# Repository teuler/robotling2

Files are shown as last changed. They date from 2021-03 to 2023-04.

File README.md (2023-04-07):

# Robotling 2

Robotling-2 is a small, simple 6-legged robot using the new Raspberry Pi micro controller [RP2040](https://www.raspberrypi.org/documentation/rp2040/getting-started/) as brain. To move around, it uses a simplified tripod walk that requires only three servo motors - inspired by a 20 year old book called ["Insectronics"](https://books.google.de/books/about/Insectronics.html?id=dYZ-67WxUWkC&redir_esc=y). Except from the electronics and a few screws, it is fully 3D printed. Software is available for [MicroPython](https://github.com/teuler/robotling2/tree/main/code/micropython) and [MMBasic](https://github.com/teuler/robotling2/tree/main/code/mmbasic).

Check out the [Wiki](https://github.com/teuler/robotling2/wiki) for details and [video1](https://youtu.be/0tkTgc_Hvlo), [video2](https://youtu.be/2amrnnNkvMk), and [video3](https://youtu.be/FfbP-4b5n9o).

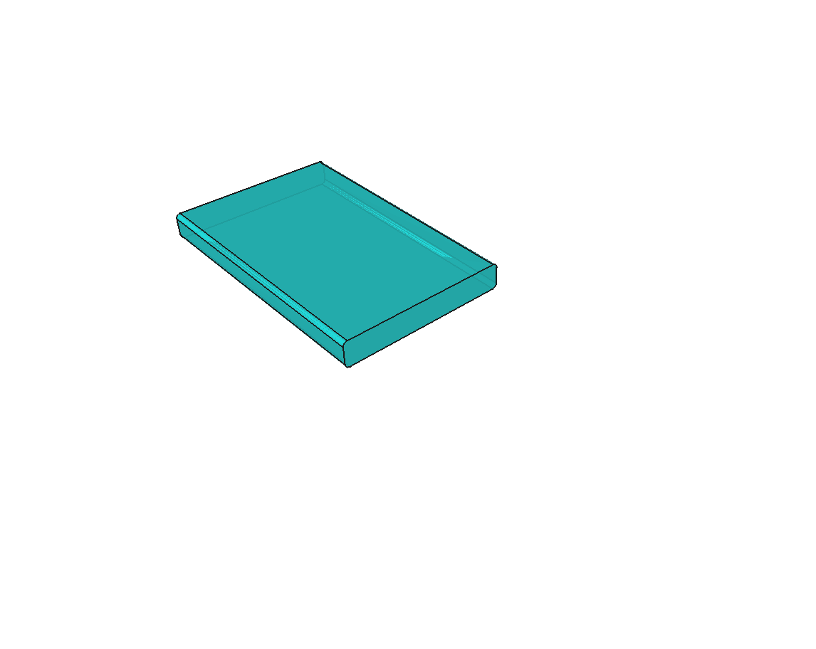
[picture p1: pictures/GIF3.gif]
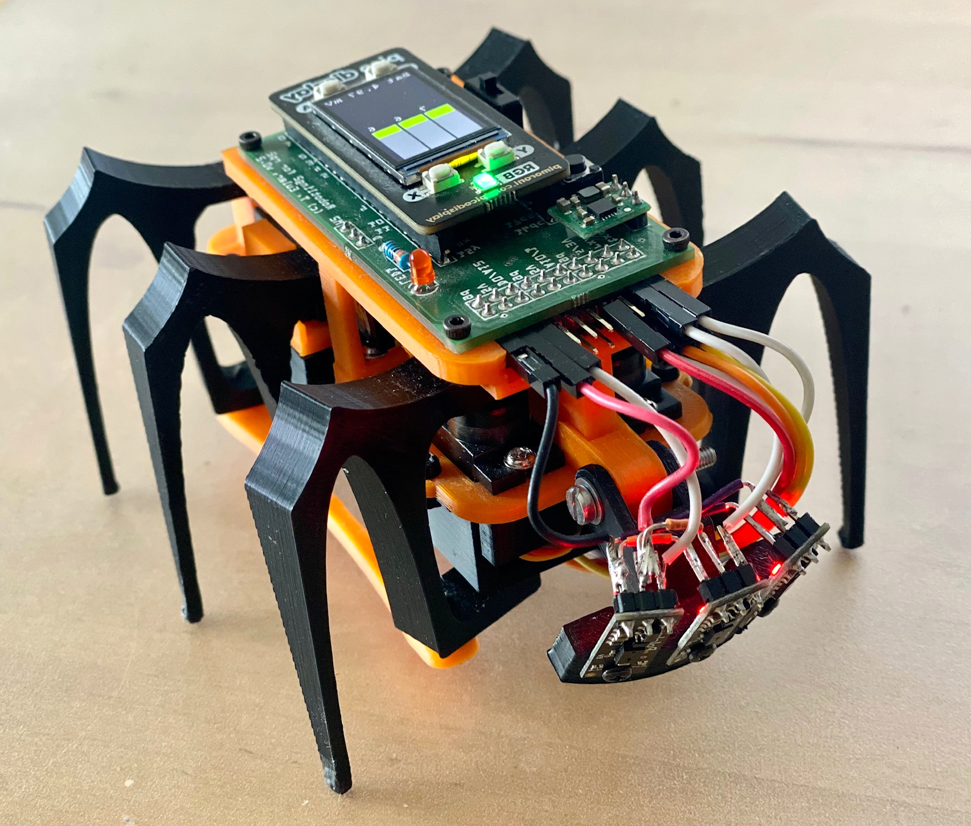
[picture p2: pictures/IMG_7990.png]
[](https://github.com/teuler/robotling2/blob/main/pictures/GIF3.gif)[](https://github.com/teuler/robotling2/blob/main/pictures/IMG_7990.png)

### CO2 watchman ("CO2-Wächter")
For the CO2-sensor version of the robot, see videos ([preview](https://www.youtube.com/watch?v=FfbP-4b5n9o), [building instructions](https://www.youtube.com/watch?v=BkKGJZfBE3s)). The robot is featured in an [article](https://www.heise.de/select/make/2023/2/2304416150000430138) in the German Make Magazin 2/23]. For the MMBasic code, see [here](https://github.com/teuler/robotling2/blob/main/code/mmbasic).

### Release Notes

* 2023-04-07
  - [Servo calibration program](https://github.com/teuler/robotling2/blob/main/code/mmbasic/rbl_servo_calibration.bas) in MMBasic added. For more information, see [here](https://github.com/teuler/robotling2/wiki/Demo#mmbasic).
* 2023-04-01
  - Own wiki page for MMBasic [robot API](https://github.com/teuler/robotling2/wiki/Robotling-API-(MMBasic))
  - Now MMBasic program versions that use the new `LIBRARY` function
* 2023-03-09
  - Carsten Wartmann's [mod](https://github.com/teuler/robotling2/tree/main/mods/c_wartmann) added
* 2023-03-04
  - MMBasic code updated: `Q` now stops program gracefully, Servo-Pin handling in one place at the end of the program (see also [here](https://github.com/teuler/robotling2/wiki/Kommentare-zum-MMBasic-Programm#hinweise-zu-servo-pin-belegung).
  - Some edits in the Wiki
* 2023-02-18
  - Replacing the Pololu voltage regulator U1V10F5, which is no longer available, by the type U3V16F5. Unfortunately, this is not a simple drop-in replacement, as the `VIn` and `VOut` are swapped. See [instructions](https://github.com/teuler/robotling2/wiki/Design-and-assembly-notes#voltage-regulator-module).
  - New versions of the [MMBasic code (v1.1x)](https://github.com/teuler/robotling2/blob/main/code/mmbasic).
  - Added new [video](https://youtu.be/FfbP-4b5n9o).
* 2023-01-01
  - MMBasic code for CO2 watchman version of the robot added.
  - `.stl' files for CO2 guard added (sensor, servo and display holders); updated FreeCAD file added.
  - New [wiki page](https://github.com/teuler/robotling2/wiki/CO2-W%C3%A4chter) on the CO2 watchman added.
* 2022-07-02
  - Code updates to account for the new [unified display API](https://github.com/pimoroni/pimoroni-pico/blob/main/micropython/modules/picographics/README.md) in the MicroPython v1.19 firmware (beta) from Pimorono
* 2022-04-15
  - New version of the [driver](https://github.com/teuler/robotling2/blob/main/code/micropython/robotling_lib/sensors/pololu_tof_ranging_pio.py) for Pololu time-of-flight sensors w/ pulse width modulation. It uses the RP2040’s PIO (programmable I/O) interface instead of waiting for `time_pulse_us()`.
* 2022-04-08
  - [MicroPython demo code](https://github.com/teuler/robotling2/tree/main/code/micropython) updated:
     - Fixed small compatibility issues with MicroPython v1.18
     - Display distance measurements also for Pololu ToF sensors   
     - Add `"display"` as a "device" to the configuration to allow the robot to operate also w/o a PicoDisplay and to prepare the use of other types of displays.
     - [Servo calibration program](https://github.com/teuler/robotling2/blob/main/code/micropython/calibrate_servos.py) added. For instructions, see [here](https://github.com/teuler/robotling2/wiki/Demo#kalibrierung-der-beinstellung).
* 2022-02-12
  - New version of [MicroPython demo code](https://github.com/teuler/robotling2/tree/main/code/micropython). Changes:
     - More consistent with MMBasic demo
     - Support for 3-channel time-of-flight distance sensor array
     - More gracefully ending the program when `X` is pressed
     - Constants for sensor port pins
     - Robot can now backup to avoid an obstacle
  - All `.stl` files adjusted to print orientation; `.stl` file for Pololu tof sensors added
  - Wiki pages added: "[Mechanik](https://github.com/teuler/robotling2/wiki/Mechanik)", "[Aufbau und Hinweise zum Zusammenbau](https://github.com/teuler/robotling2/wiki/Aufbau-und-Hinweise-zum-Zusammenbau)", German version of "[Elektronik, Platine, und Teile](https://github.com/teuler/robotling2/wiki/Elektronik,-Platine,-und-Teile)", "[Erweiterungen & Modifikationen](https://github.com/teuler/robotling2/wiki/Erweiterungen-&-Modifikationen)", "[Sensoren](https://github.com/teuler/robotling2/wiki/Sensoren)"
  - Cleaned up and updated wiki pages for MicroPython and MMBasic
  - Added demo code loading instructions for both [MMBasic](https://github.com/teuler/robotling2/wiki/Running-the-robot-with-MMBasic) and [MicroPython](https://github.com/teuler/robotling2/wiki/Running-the-robot-with-MicroPython).
  - Completed parts list
* 2022-01-22
  - [Parts list](https://github.com/teuler/robotling2/wiki/Electronics,-PCB-and-parts#Electronics_Parts) added 
  - Information about the distance sensors added
* 2021-12-16
  - Slightly updated version of board added
* 2021-11-20
  - [MMBasic program explained (German)](https://github.com/teuler/robotling2/wiki/Kommentare-zum-MMBasic-Programm) added to Wiki.
* 2021-11-07
  - Code v1.xx written in [MMBasic](https://mmbasic.com/) added. It uses the Pico version (["PicoMite"](https://geoffg.net/picomite.html)) version of the MMBasic interpreter written Geoff Graham and Peter Mather (see [repository](https://github.com/UKTailwind/PicoMite)).
  - New [wiki page](https://github.com/teuler/robotling2/wiki/Running-the-robot-with-MMBasic) about running the robot under MMBasic.
  - New sensor head for Time-of-flight distance sensors by Pololu [#4064](https://www.pololu.com/product/4064/specs)
* 2021-04-25
  - "Arm" for distance sensor added (i.e. the [multi-pixel evo mini](https://www.terabee.com/shop/lidar-tof-range-finders/teraranger-evo-mini/))
  - Battery compartment modified such that it can also carry a [1000 mAh single-cell LiPo](https://www.exp-tech.de/zubehoer/batterien-akkus/lipo-akkus/5801/3.7v-1000mah-lithium-polymer-akku-mit-jst-ph-anschluss).
* 2021-04-10
  - PCB slightly updated
  - Video and new pictures added
* 2021-04-05
  - Fritzing file and BOM for board (v0.3) added
  - .STL files for 3D printed parts added
  - FreeCAD document added
  - Some code added (so far only walk demo w/o sensors)
* 2021-03-27 - Initial release

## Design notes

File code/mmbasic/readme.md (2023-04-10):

## Versions

### Stand-alone program versions

- `rbl2_v1_13_co2.bas`  
  Full version w/ CO2 sensor, ToF distance sensors, 240x240 display, and 4th servo. Sleeps until the CO2 concentration is above a certain limit. If it is, the robot wakes up and walks around.
- `rbl2_v1_12_tof_picodisplay.bas`  
  Version w/ ToF distance sensors, and 240x135 display (PicoDisplay). Walks around, avoiding obstacles and cliffs/edges.
- `rbl2_v1_11_basic`  
  Basic version (no sensors, no display). Walks in a square (sort of). Will run into obstacles or fall of the table!
  
### Program versions using `rbl_lib`

The current beta version of MMBasic (`PicoMiteV5.07.07b33.uf2` and higher; [download](https://geoffg.net/picomite.html)) implements `LIBRARY` commands, which allow to "extend" MMBasic with a set of functions (in form of another `.bas` program). Multiple libraries can be used and they occupy the flash slot #4. By moving all robot functions and subroutines (`R.xxx`) into a library, the programs become much shorter and common functions (now in the library) are much easier to maintain between programs. To demonstrate this, I converted the two of the demo programs such that they use a common library.

- `rbl2_v1_21_basic`, `rbl2_v1_22_tof_picodisplay.bas`  
  Library-enabled versions of the programs above. 
- `rbl_lib.bas`  
  Library with all robot-related functions, subroutines, constants, and variables.
- `rbl_servo_calibration.bas`  
  Interactive servo calibration program.

To use the new programs:
- Load library `rbl_lib.bas` onto the Pico using `xmodem r`, then:
     ```
     flash overwrite 3  ' Save original library code
     library delete     ' Delete previous libraries 
     library save       ' Save current code as library
     ```
- When saving as library, the code is stripped of all extra stuff (e.g. comments, white spaces etc.). To make a change to the original library code, use the copy in flash slot #3. Don't forget to save your main program before you load the library into the editor:
     ```
     flash overwrite 1  ' Save main program, if any, in slot #1
     flash load 3       ' Load original library code from slot #3
     edit               ' Make your changes
     flash overwrite 3  ' Save changed library code
     library delete     ' Delete previous libraries
     library save       ' Save current code as library
     ```

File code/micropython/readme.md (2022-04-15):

> Note: _The folder `robotling_lib` contains only a minimum of drivers; for more drivers, see [robotling_lib](https://github.com/teuler/robotling_lib)._

### TODOs
- Add splash screen

### Issues
- The current MicroPython firmware (v1.18) for the Pico seems to crash from time to time; it is still responsible but shows nonsense errors (`NotImplementedError: opcode`). In this case, a reset helps.

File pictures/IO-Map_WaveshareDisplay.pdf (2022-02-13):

Pin | Funktion | Waveshare-
Display | Robotling | Robotling neu
1 | GP0 | | I2C0 SD
2 | GP1 | | I2C0 SCL
3 | GND
4 | GP2 | Joy U | M2 PWM
5 | GP3 | Joy S | D0 | X-Shut Links
6 | GP4 | | Tx
7 | GP5 | | Rx
8 | GND
9 | GP6 | | | M2 PWM
10 | GP7 | | | M1 PWM
11 | GP8 | Data/Cmd
12 | GP9 | SPI CS | D2-J4
13 | GND
14 | GP10 | SPI Clk | M1 PWM
15 | GP11 | SPI Data | LED
16 | GP12 | Reset
17 | GP13 | BL
18 | GND
19 | GP14 | | | D2-J4
20 | GP15 | A
21 | GP16 | Joy L
22 | GP17 | B
23 | GND
24 | GP18 | Joy D
25 | GP19 | | | LED
26 | GP20 | Joy R
27 | GP21 | | M3 PWM
28 | GND
29 | GP22 | | D1 | X-Shut Rechts
30 | Run
31 | GP26 | | Ai0
32 | GP27 | | Ai1
33 | GND
34 | GP28 | | Ai2
35 | ADCref
36 | 3V3Out | | 3V
37 | 3V3_En
38 | GND
39 | Vsys
40 | Vbus
| LED
| Bat

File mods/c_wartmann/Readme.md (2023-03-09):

## Robotling2 für Blender

Kontakt: Carsten, caw beim make-magazin.de

Übersicht |
:--|
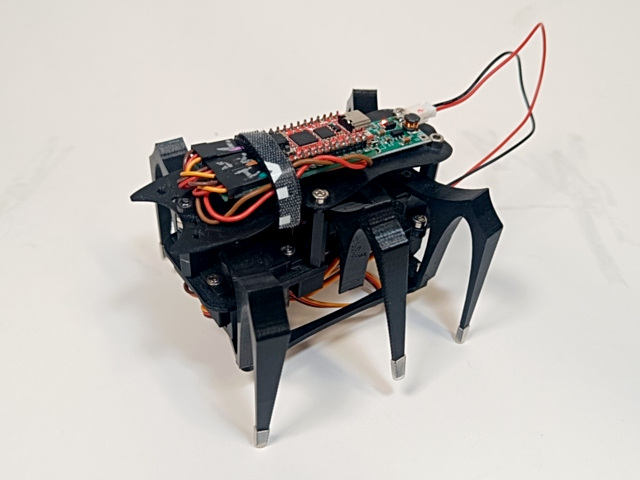
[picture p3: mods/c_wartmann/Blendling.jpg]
[](https://github.com/teuler/robotling2/blob/main/mods/c_wartmann/Blendling.jpg)

* In Blender importiert für die Blenderheads
* "Freestyle" ohne Platine
* Insektoides Design der der oberen Platte, mehr Platz für Experimente
* Ein kleiner USB-ladbarer LiIon Akku passt inkl. Halter zwischen die Beine
* Keine Kugellager, stattdessen dienen mehr M2 Schrauben als "Lager" 
* M3 Nylon Standoffs als Abstandhalter

Von unten |
:--|
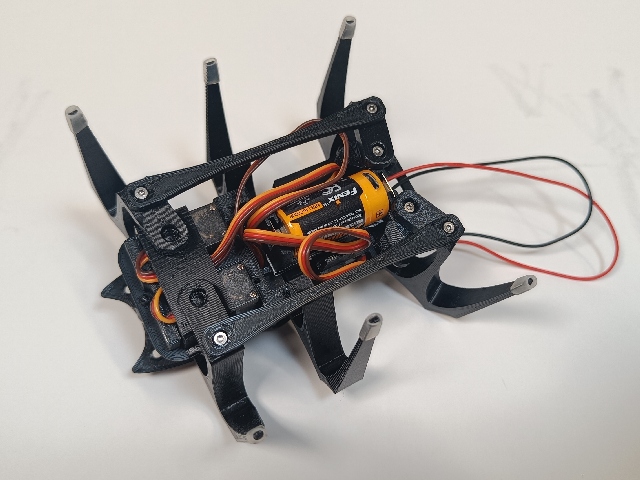
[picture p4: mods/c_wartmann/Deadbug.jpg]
[](https://github.com/teuler/robotling2/blob/main/mods/c_wartmann/Deadbug.jpg)

In Blender |
:--|
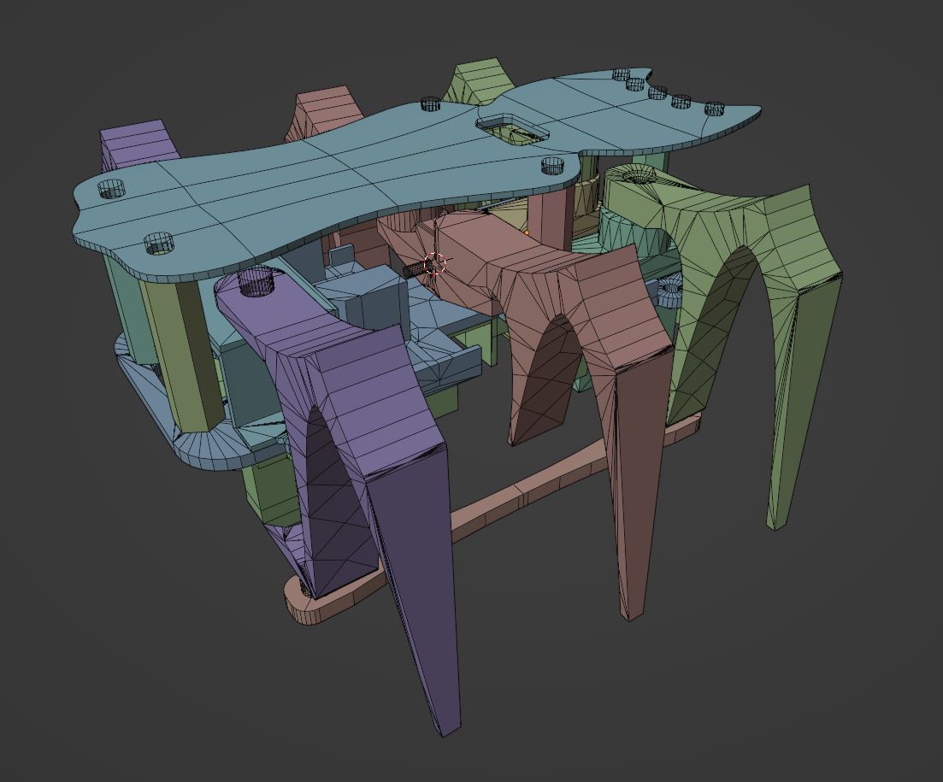
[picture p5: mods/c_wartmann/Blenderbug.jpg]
[](https://github.com/teuler/robotling2/blob/main/mods/c_wartmann/Blenderbug.jpg)

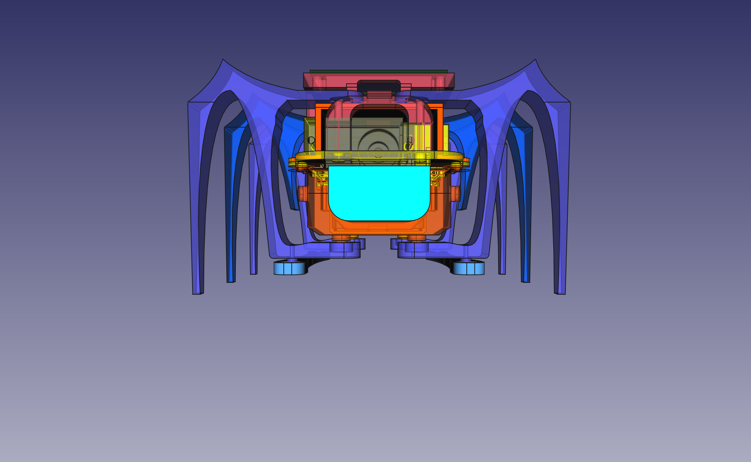
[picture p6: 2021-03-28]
pictures/back.png

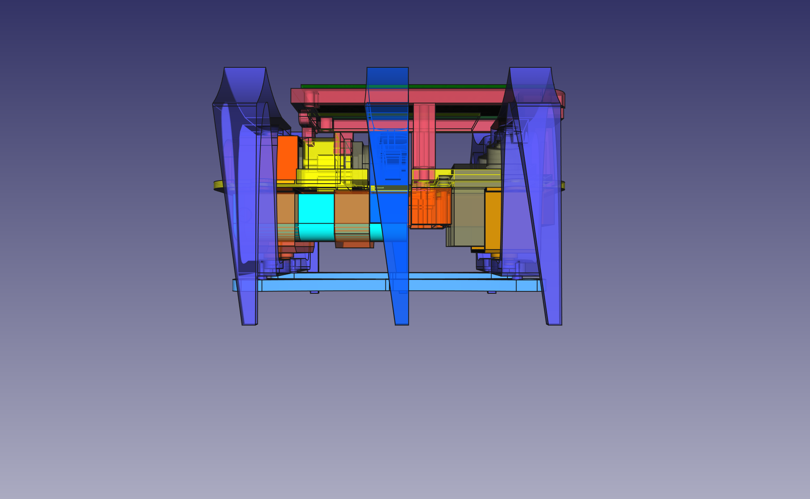
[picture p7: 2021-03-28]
pictures/side.png

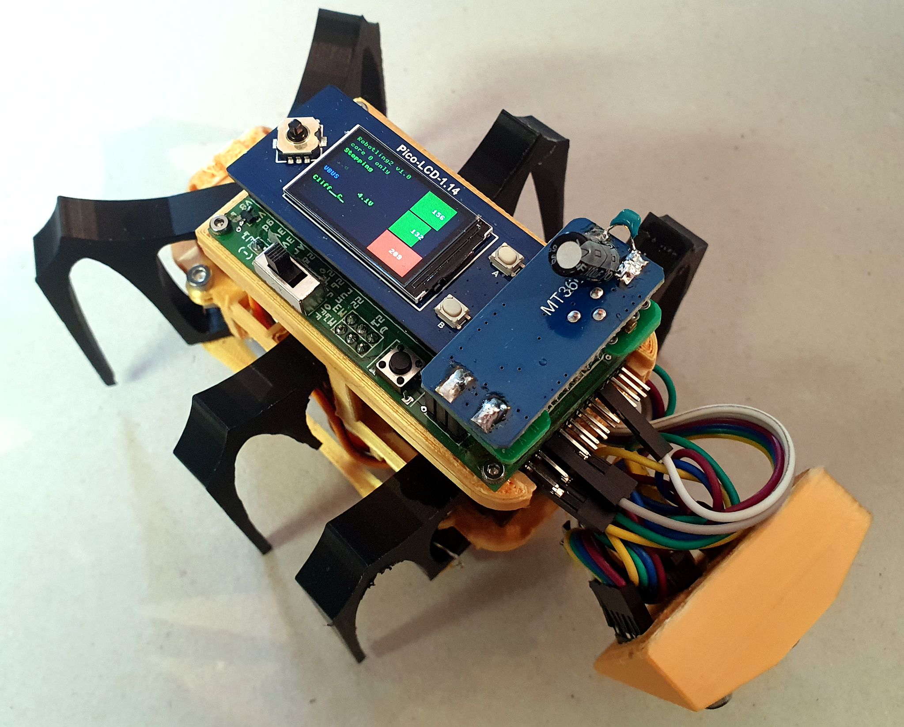
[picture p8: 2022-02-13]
pictures/Bild4_C_Otto.jpg

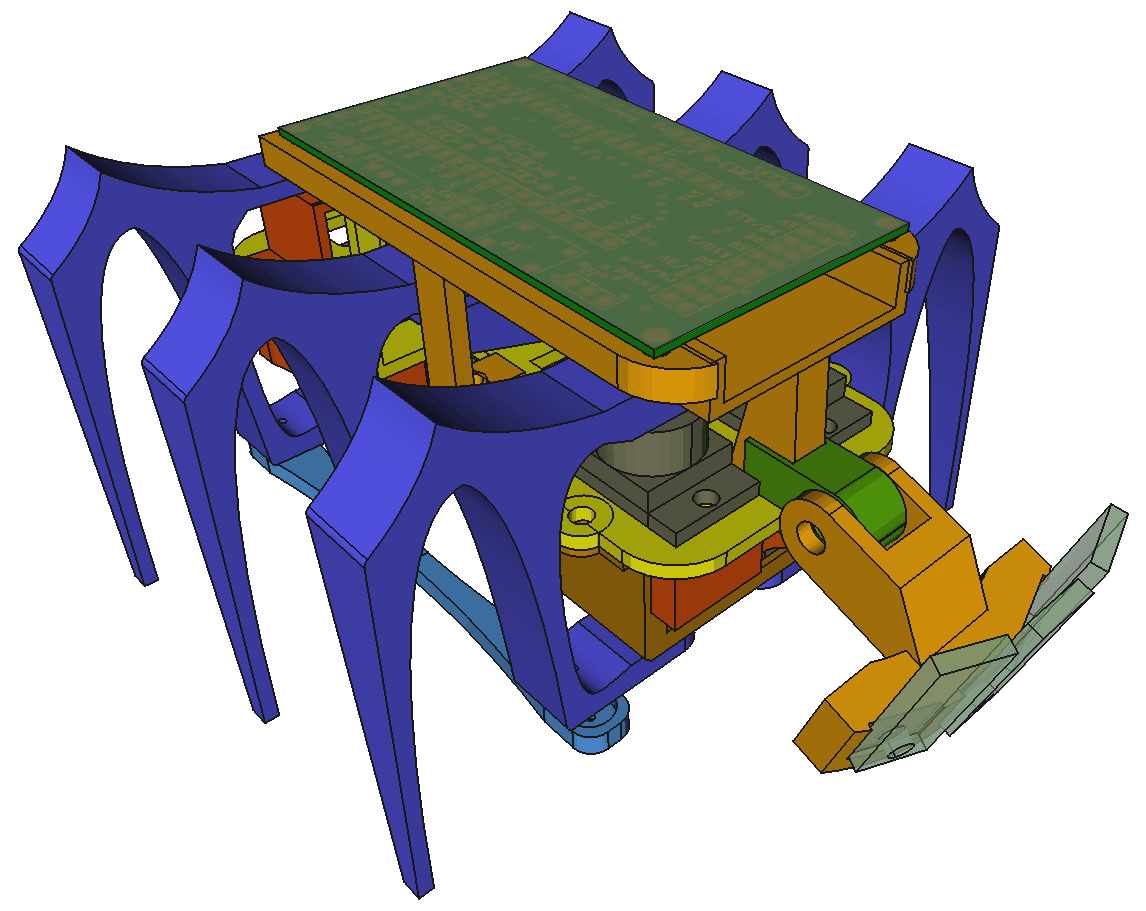
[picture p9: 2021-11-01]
pictures/Full.png

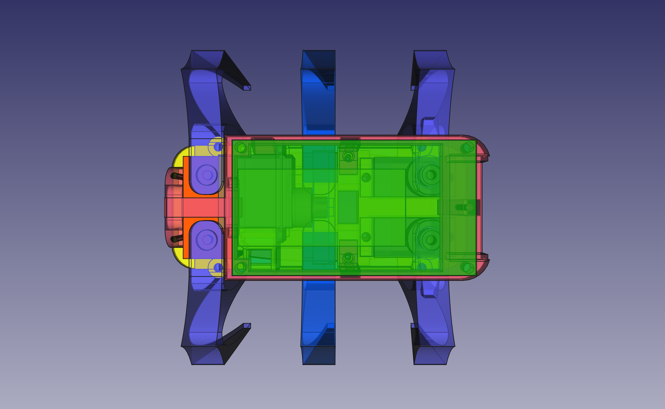
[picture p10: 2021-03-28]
pictures/top.png

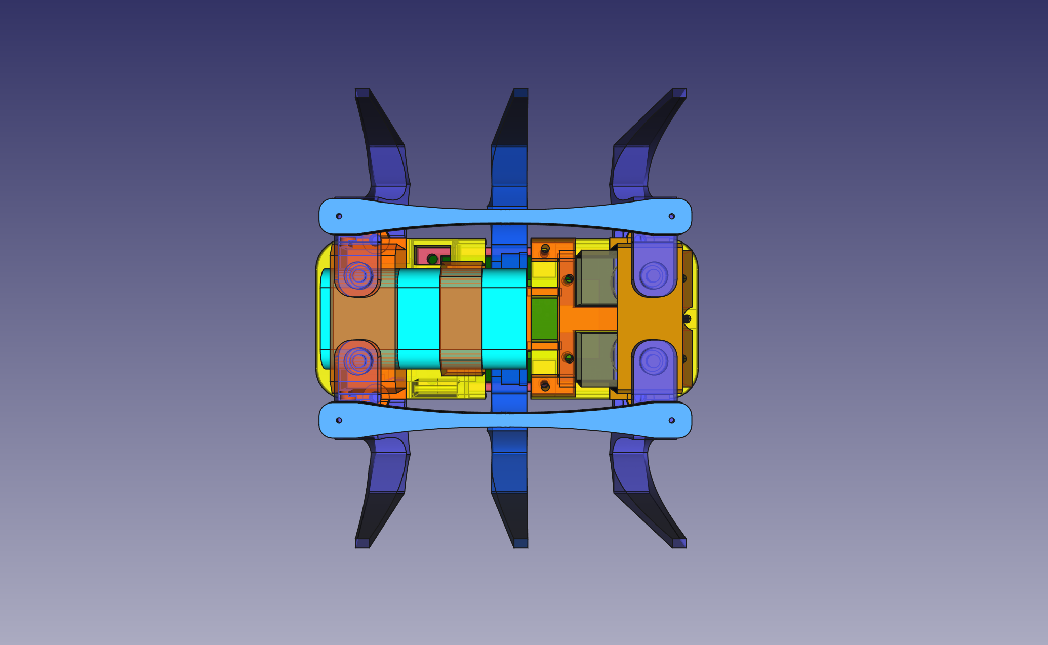
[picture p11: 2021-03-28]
pictures/bottom.png

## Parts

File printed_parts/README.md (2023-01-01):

This folder contains the `.stl` files for all parts. The robot was desiged using [FreeCad](https://www.freecadweb.org/); the corresponding design files (different versions) are in the  `FreeCAD_files` subfolder. 

The subfolder `deprecated` contains older parts.

The subfolder `mods_c_otto` contains parts contributed by **Carsten Otto**.

### Notes:
- `bar.stl`, `bar_long.stl`, `bar_medium.stl`<br>
  Only one of these is needed. They have different lengths, defining if the legs are parallel to each other (`bar`) or if the front and rear legs are angled slightly forwards and backwards, respectively (`bar_long`, `bar_medium`)
- `rear_bottom.stl` (in deprecated), `rear_bottom_lipo1000.stl`<br> 
  Only one of these is needed, depending on the battery holder. `rear_bottom` holds a 2x AAA battery cartridge (not recommended, because the batteries wear out quite quickly), `rear_bottom_lipo1000` a approx. 1Ah LiPo (e.g. like [this](https://eckstein-shop.de/LiPo-Akku-Lithium-Ion-Polymer-Batterie-37V-1200mAh-JST-PH-Connector)).
- `sensor_adapter_evo_mini_terabee.stl`<br> 
  This part is needed to attached an [Evo Mini](https://www.terabee.com/shop/lidar-tof-range-finders/teraranger-evo-mini/) ranging sensor from Terabee.
- `sensor_adapter_tof_pololu.stl`<br>
  This part is needed to attach Pololu's time-of-flight distance sensors (for details, see [here](https://github.com/teuler/robotling2/wiki/Sensoren#time-of-flight-sensoren)).
- `board_carrier_v2.stl`<br>
  Allows for easier connecting the USB cable to the Pico.
- `screen_holder.stl`, `sensor_bank_scd41.stl`, `servo_holder.stl`<br> 
  Parts needed for the CO2 guard version of the robot. `servo_holder.stl` is mounted at the front of the PCB frame to hold a micro servo, which raises a display. `screen_holder.stl` holds this display and is mounted on the servo arm. Finally, `sensor_bank_scd41.stl` sits at the back of the PCB frame and allows to mount the SCD41 breakout containing the CO2 / temperature / humidity sensor.

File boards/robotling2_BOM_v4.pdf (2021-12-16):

# Bill of Materials: robotling2_v4.fzz

H:\Dropbox\__ROS\__Circuit boards\board_robotling2\robotling2_v4.fzz
Donnerstag, Dezember 16 2021, 09:49:42

# Assembly List

Label | Part Type | Properties
Ai0/1 | Generic male header - 3 pins | Beinchen 3; Form ♂ (male); Lochgröße 1.0mm,0.508mm; row single; Paket THT; Beinchenabstand 0.1in (2.54mm)
Ai1 | Generic male header - 3 pins | Beinchen 3; Form ♂ (male); Lochgröße 1.0mm,0.508mm; row single; Paket THT; Beinchenabstand 0.1in (2.54mm)
D0/Ai2 | Generic male header - 3 pins | Beinchen 3; Form ♂ (male); Lochgröße 1.0mm,0.508mm; row single; Paket THT; Beinchenabstand 0.1in (2.54mm)
I2C | Generic male header - 4 pins | Beinchen 4; Form ♂ (male); Lochgröße 1.0mm,0.508mm; row single; Paket THT; Beinchenabstand 0.1in (2.54mm)
I2C1 | Generic male header - 4 pins | Beinchen 4; Form ♂ (male); Lochgröße 1.0mm,0.508mm; row single; Paket THT; Beinchenabstand 0.1in (2.54mm)
I2C2 | Header 4 | Paket 1x04-1mm-ra; Variante smd2
J1 | Generic male header - 2 pins | Beinchen 2; Form ♂ (male); Lochgröße 1.0mm,0.508mm; row single; Paket THT; Beinchenabstand 0.1in (2.54mm)
J2 | Generic female header

### - 3 pins

| | Beinchen 3; Form ♀ (female); Lochgröße 1.0mm,0.508mm; row single; Paket THT; Beinchenabstand 0.1in (2.54mm)
J2 | Generic male header - 3 pins | Beinchen 3; Form ♂ (male); Lochgröße 1.0mm,0.508mm; row single; Paket THT; Beinchenabstand 0.1in (2.54mm)
J3 | Generic male header - 3 pins | Beinchen 3; Form ♂ (male); Lochgröße 1.0mm,0.508mm; row single; Paket THT; Beinchenabstand 0.1in (2.54mm)
J4 | Generic male header - 3 pins | Beinchen 3; Form ♂ (male); Lochgröße 1.0mm,0.508mm; row single; Paket THT; Beinchenabstand 0.1in (2.54mm)
J5 | Generic female header

### - 20 pins

| | Beinchen 20; Form ♀ (female); Lochgröße 1.0mm,0.508mm; row single; Paket THT; Beinchenabstand 0.1in (2.54mm)
J6 | Generic female header

### - 20 pins

| | Beinchen 20; Form ♀ (female); Lochgröße 1.0mm,0.508mm; row single; Paket THT; Beinchenabstand 0.1in (2.54mm)
LED1 | Yellow (595nm) LED | Farbe Yellow (595nm); Strom 0.030; Paket 3 mm [THT]; leg yes
Fritzing Bill of Materials | file:///H:/Dropbox/__GIT/robotling2/boards/robotling2_v4_bom.html
1 von 3 | 16.12.2021, 09:50

Label | Part Type | Properties
M1 | Generic male header - 3 pins | Beinchen 3; Form ♂ (male); Lochgröße 1.0mm,0.508mm; row single; Paket THT; Beinchenabstand 0.1in (2.54mm)
M2 | Generic male header - 3 pins | Beinchen 3; Form ♂ (male); Lochgröße 1.0mm,0.508mm; row single; Paket THT; Beinchenabstand 0.1in (2.54mm)
M3 | Generic male header - 3 pins | Beinchen 3; Form ♂ (male); Lochgröße 1.0mm,0.508mm; row single; Paket THT; Beinchenabstand 0.1in (2.54mm)
Mod1 | Raspberry Pi Pico | Typ tht; Variante variant 1
Q1 | PNP-Transistor | Paket SOT-23 [SMD]; Typ PNP
R1 | 1kΩ Resistor | bands 4; Toleranz ±5%; Leistung 0.25; Paket THT; Beinchenabstand 400 mil; Widerstand 1kΩ
R2 | 1.5kΩ Resistor | bands 4; Toleranz ±5%; Leistung 0.25; Paket THT; Beinchenabstand 400 mil; Widerstand 1.5kΩ
R3 | 1kΩ Resistor | bands 4; Toleranz ±5%; Leistung 0.25; Paket THT; Beinchenabstand 400 mil; Widerstand 1kΩ
R4 | 1kΩ Resistor | bands 4; Toleranz ±5%; Leistung 0.25; Paket THT; Beinchenabstand 400 mil; Widerstand 1kΩ
R5 | 1.5kΩ Resistor | bands 4; Toleranz ±5%; Leistung 0.25; Paket THT; Beinchenabstand 400 mil; Widerstand 1.5kΩ
R6 | 1.5kΩ Resistor | bands 4; Toleranz ±5%; Leistung 0.25; Paket THT; Beinchenabstand 400 mil; Widerstand 1.5kΩ
R7 | 8.2kΩ Resistor | bands 4; Toleranz ±5%; Leistung 0.25; Paket THT; Beinchenabstand 400 mil; Widerstand 8.2kΩ
R8 | 8.2kΩ Resistor | bands 4; Toleranz ±5%; Leistung 0.25; Paket THT; Beinchenabstand 400 mil; Widerstand 8.2kΩ
R9 | 220Ω Resistor | bands 4; Toleranz ±5%; Leistung 0.25; Paket THT; Beinchenabstand 400 mil; Widerstand 220Ω
S1 | SPST Switch | Paket switch-spdt_lock.007s; Variante pth_lock
S2 | Momentary Switch | Paket ksa_sealed_tac_switch; Variante ksa_sealed

# Shopping List

Amount | Part Type | Properties
9 | Generic male header - 3 pins | Beinchen 3; Form ♂ (male); Lochgröße 1.0mm,0.508mm; row single; Paket THT; Beinchenabstand 0.1in (2.54mm)
2 | Generic male header - 4 pins | Beinchen 4; Form ♂ (male); Lochgröße 1.0mm,0.508mm; row single; Paket THT; Beinchenabstand 0.1in (2.54mm)

Amount | Part Type | Properties
1 | Header 4 | Paket 1x04-1mm-ra; Variante smd2
1 | Generic male header - 2 pins | Beinchen 2; Form ♂ (male); Lochgröße 1.0mm,0.508mm; row single; Paket THT; Beinchenabstand 0.1in (2.54mm)
1 | Generic female header

### - 3 pins

| | Beinchen 3; Form ♀ (female); Lochgröße 1.0mm,0.508mm; row single; Paket THT; Beinchenabstand 0.1in (2.54mm)
2 | Generic female header

### - 20 pins

| | Beinchen 20; Form ♀ (female); Lochgröße 1.0mm,0.508mm; row single; Paket THT; Beinchenabstand 0.1in (2.54mm)
1 | Yellow (595nm) LED | Farbe Yellow (595nm); Strom 0.030; Paket 3 mm [THT]; leg yes
1 | Raspberry Pi Pico | Typ tht; Variante variant 1
1 | PNP-Transistor | Paket SOT-23 [SMD]; Typ PNP
3 | 1kΩ Resistor | bands 4; Toleranz ±5%; Leistung 0.25; Paket THT; Beinchenabstand 400 mil; Widerstand 1kΩ
3 | 1.5kΩ Resistor | bands 4; Toleranz ±5%; Leistung 0.25; Paket THT; Beinchenabstand 400 mil; Widerstand 1.5kΩ
2 | 8.2kΩ Resistor | bands 4; Toleranz ±5%; Leistung 0.25; Paket THT; Beinchenabstand 400 mil; Widerstand 8.2kΩ
1 | 220Ω Resistor | bands 4; Toleranz ±5%; Leistung 0.25; Paket THT; Beinchenabstand 400 mil; Widerstand 220Ω
1 | SPST Switch | Paket switch-spdt_lock.007s; Variante pth_lock
1 | Momentary Switch | Paket ksa_sealed_tac_switch; Variante ksa_sealed

Exported with Fritzing 0.9.9- http://fritzing.org

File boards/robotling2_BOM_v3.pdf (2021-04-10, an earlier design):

# Bill of Materials: robotling2_v3.fzz

G:/Dropbox/__ROS/__Circuit boards/board_robotling2/robotling2_v3.fzz
Samstag, April 10 2021, 10:02:25

# Assembly List

Label | Part Type | Properties
Ai0/1 | Generic male header - 3 pins | Beinchenabstand 0.1in (2.54mm); Paket THT; Beinchen 3; Form ♂ (male); Lochgröße 1.0mm,0.508mm; row single
Ai1 | Generic male header - 3 pins | Beinchenabstand 0.1in (2.54mm); Paket THT; Beinchen 3; Form ♂ (male); Lochgröße 1.0mm,0.508mm; row single
D0/Ai2 | Generic male header - 3 pins | Beinchenabstand 0.1in (2.54mm); Paket THT; Beinchen 3; Form ♂ (male); Lochgröße 1.0mm,0.508mm; row single
I2C | Generic male header - 4 pins | Beinchenabstand 0.1in (2.54mm); Paket THT; Beinchen 4; Form ♂ (male); Lochgröße 1.0mm,0.508mm; row single
I2C1 | Generic male header - 4 pins | Beinchenabstand 0.1in (2.54mm); Paket THT; Beinchen 4; Form ♂ (male); Lochgröße 1.0mm,0.508mm; row single
I2C2 | Header 4 | Paket 1x04-1mm-ra; Variante smd2
J1 | Generic male header - 2 pins | Beinchenabstand 0.1in (2.54mm); Paket THT; Beinchen 2; Form ♂ (male); Lochgröße 1.0mm,0.508mm; row single
J2 | Generic female header

### - 3 pins

| | Beinchenabstand 0.1in (2.54mm); Paket THT; Beinchen 3; Form ♀ (female); Lochgröße 1.0mm,0.508mm; row single
J2 | Generic male header - 3 pins | Beinchenabstand 0.1in (2.54mm); Paket THT; Beinchen 3; Form ♂ (male); Lochgröße 1.0mm,0.508mm; row single
J3 | Generic male header - 3 pins | Beinchenabstand 0.1in (2.54mm); Paket THT; Beinchen 3; Form ♂ (male); Lochgröße 1.0mm,0.508mm; row single
J5 | Generic female header

### - 20 pins

| | Beinchenabstand 0.1in (2.54mm); Paket THT; Beinchen 20; Form ♀ (female); Lochgröße 1.0mm,0.508mm; row single
J6 | Generic female header

### - 20 pins

| | Beinchenabstand 0.1in (2.54mm); Paket THT; Beinchen 20; Form ♀ (female); Lochgröße 1.0mm,0.508mm; row single
LED1 | Yellow (595nm) LED | Farbe Yellow (595nm); Paket 3 mm [THT]; Strom 0.030; leg yes
M1 | Generic male header - 3 pins | Beinchenabstand 0.1in (2.54mm); Paket THT; Beinchen 3; Form ♂ (male); Lochgröße 1.0mm,0.508mm; row single
Fritzing Bill of Materials | file:///G:/Dropbox/__GIT/robotling2/pictures/robotling2_v3_bom.html
1 von 3 | 10.04.2021, 10:03

Label | Part Type | Properties
M2 | Generic male header - 3 pins | Beinchenabstand 0.1in (2.54mm); Paket THT; Beinchen 3; Form ♂ (male); Lochgröße 1.0mm,0.508mm; row single
M3 | Generic male header - 3 pins | Beinchenabstand 0.1in (2.54mm); Paket THT; Beinchen 3; Form ♂ (male); Lochgröße 1.0mm,0.508mm; row single
Mod1 | Raspberry Pi Pico | Typ tht; Variante variant 1
Q1 | PNP-Transistor | Typ PNP; Paket SOT-23 [SMD]
R1 | 1kΩ Resistor | bands 4; Beinchenabstand 400 mil; Paket THT; Toleranz ±5%; Leistung 0.25; Widerstand 1kΩ
R2 | 1.5kΩ Resistor | bands 4; Beinchenabstand 400 mil; Paket THT; Toleranz ±5%; Leistung 0.25; Widerstand 1.5kΩ
R3 | 1kΩ Resistor | bands 4; Beinchenabstand 400 mil; Paket THT; Toleranz ±5%; Leistung 0.25; Widerstand 1kΩ
R4 | 1kΩ Resistor | bands 4; Beinchenabstand 400 mil; Paket THT; Toleranz ±5%; Leistung 0.25; Widerstand 1kΩ
R5 | 1.5kΩ Resistor | bands 4; Beinchenabstand 400 mil; Paket THT; Toleranz ±5%; Leistung 0.25; Widerstand 1.5kΩ
R6 | 1.5kΩ Resistor | bands 4; Beinchenabstand 400 mil; Paket THT; Toleranz ±5%; Leistung 0.25; Widerstand 1.5kΩ
R7 | 8.2kΩ Resistor | bands 4; Beinchenabstand 400 mil; Paket THT; Toleranz ±5%; Leistung 0.25; Widerstand 8.2kΩ
R8 | 8.2kΩ Resistor | bands 4; Beinchenabstand 400 mil; Paket THT; Toleranz ±5%; Leistung 0.25; Widerstand 8.2kΩ
R9 | 220Ω Resistor | bands 4; Beinchenabstand 400 mil; Paket THT; Toleranz ±5%; Leistung 0.25; Widerstand 220Ω
S1 | SPST Switch | Paket switch-spdt_lock.007s; Variante pth_lock
S2 | Momentary Switch | Paket ksa_sealed_tac_switch; Variante ksa_sealed

# Shopping List

Amount | Part Type | Properties
8 | Generic male header - 3 pins | Beinchenabstand 0.1in (2.54mm); Paket THT; Beinchen 3; Form ♂ (male); Lochgröße 1.0mm,0.508mm; row single
2 | Generic male header - 4 pins | Beinchenabstand 0.1in (2.54mm); Paket THT; Beinchen 4; Form ♂ (male); Lochgröße 1.0mm,0.508mm; row single
1 | Header 4 | Paket 1x04-1mm-ra; Variante smd2

Amount | Part Type | Properties
1 | Generic male header - 2 pins | Beinchenabstand 0.1in (2.54mm); Paket THT; Beinchen 2; Form ♂ (male); Lochgröße 1.0mm,0.508mm; row single
1 | Generic female header

### - 3 pins

| | Beinchenabstand 0.1in (2.54mm); Paket THT; Beinchen 3; Form ♀ (female); Lochgröße 1.0mm,0.508mm; row single
2 | Generic female header

### - 20 pins

| | Beinchenabstand 0.1in (2.54mm); Paket THT; Beinchen 20; Form ♀ (female); Lochgröße 1.0mm,0.508mm; row single
1 | Yellow (595nm) LED | Farbe Yellow (595nm); Paket 3 mm [THT]; Strom 0.030; leg yes
1 | Raspberry Pi Pico | Typ tht; Variante variant 1
1 | PNP-Transistor | Typ PNP; Paket SOT-23 [SMD]
3 | 1kΩ Resistor | bands 4; Beinchenabstand 400 mil; Paket THT; Toleranz ±5%; Leistung 0.25; Widerstand 1kΩ
3 | 1.5kΩ Resistor | bands 4; Beinchenabstand 400 mil; Paket THT; Toleranz ±5%; Leistung 0.25; Widerstand 1.5kΩ
2 | 8.2kΩ Resistor | bands 4; Beinchenabstand 400 mil; Paket THT; Toleranz ±5%; Leistung 0.25; Widerstand 8.2kΩ
1 | 220Ω Resistor | bands 4; Beinchenabstand 400 mil; Paket THT; Toleranz ±5%; Leistung 0.25; Widerstand 220Ω
1 | SPST Switch | Paket switch-spdt_lock.007s; Variante pth_lock
1 | Momentary Switch | Paket ksa_sealed_tac_switch; Variante ksa_sealed

Exported with Fritzing 0.9.6- http://fritzing.org

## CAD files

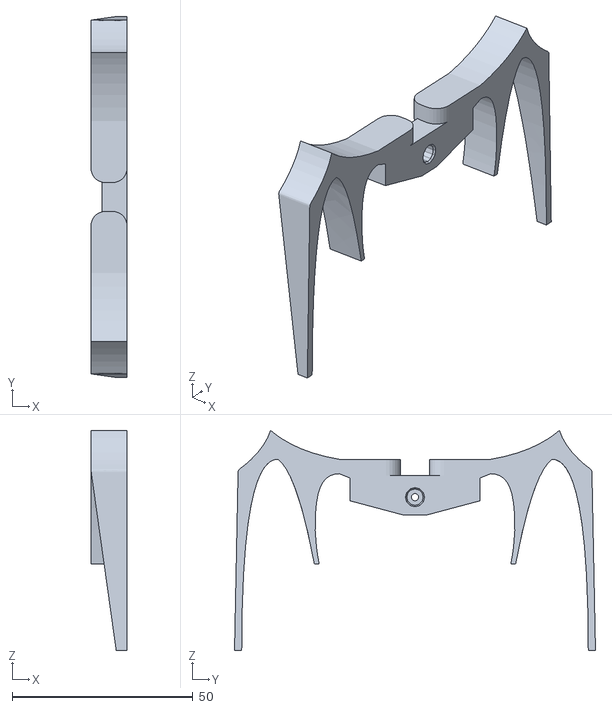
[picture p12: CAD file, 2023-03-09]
mods/c_wartmann/STL/RobaslingBlender-leg_centre_cw.stl
10.0 x 100.0 x 61.0

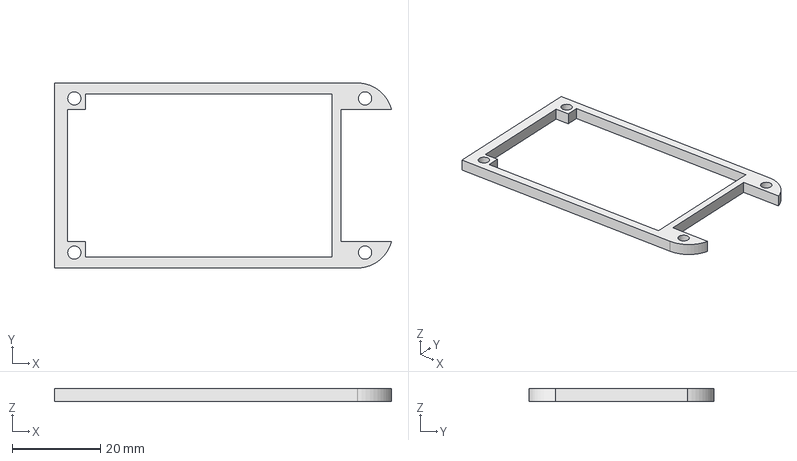
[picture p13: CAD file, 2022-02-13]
printed_parts/mods_c_otto/Adapterplatte.FCStd
76.5 x 42.0 x 3.00 mm

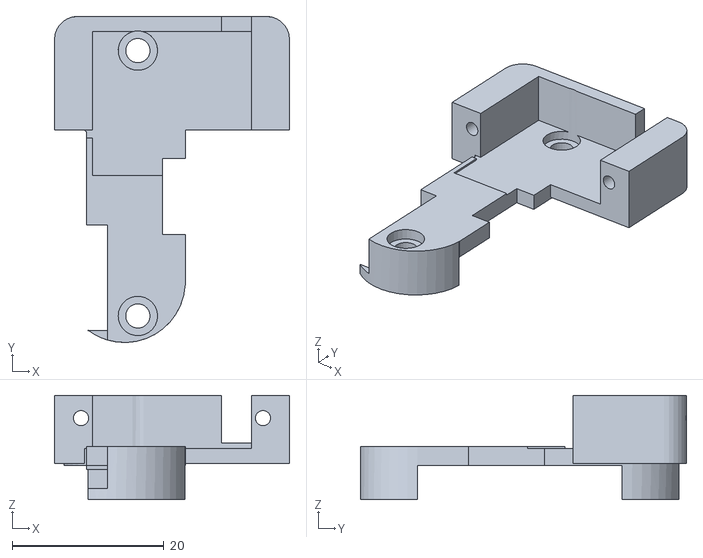
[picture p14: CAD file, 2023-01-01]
printed_parts/servo_holder.stl
31.0 x 43.0 x 13.8

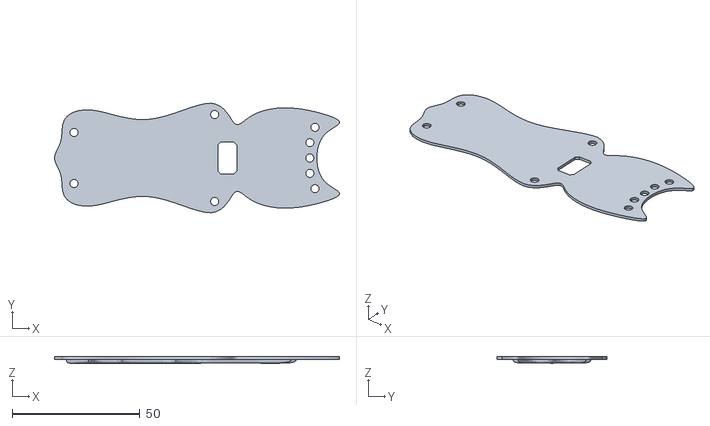
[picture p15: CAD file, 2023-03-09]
mods/c_wartmann/STL/RobaslingBlender-Akku_Platte.stl
111.5 x 42.9 x 2.56

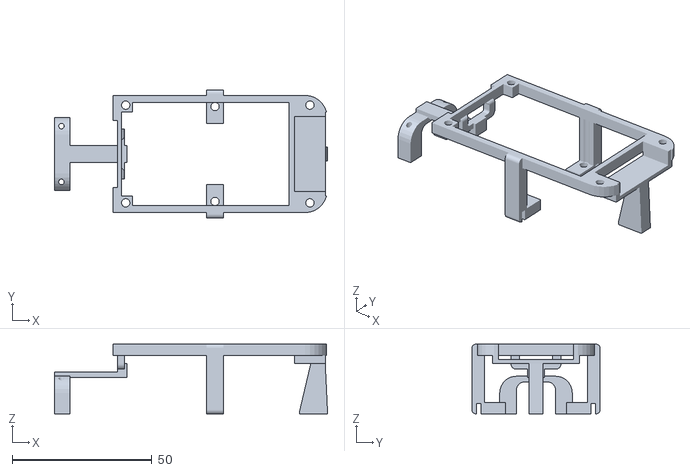
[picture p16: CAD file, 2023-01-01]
printed_parts/board_carrier_v2.stl
97.8 x 46.0 x 25.0

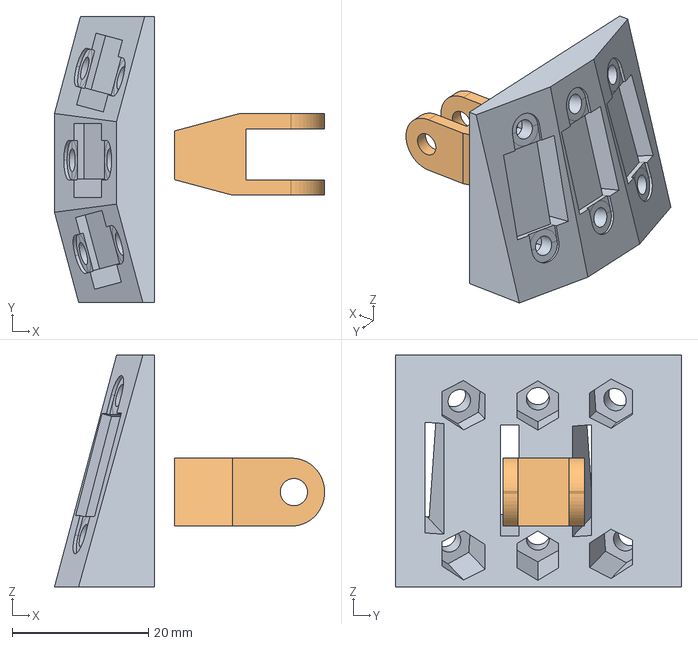
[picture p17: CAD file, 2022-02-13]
printed_parts/mods_c_otto/ToF Sensor.FCStd
39.7 x 42.0 x 34.0 mm
Sensorhalter
Verbinder

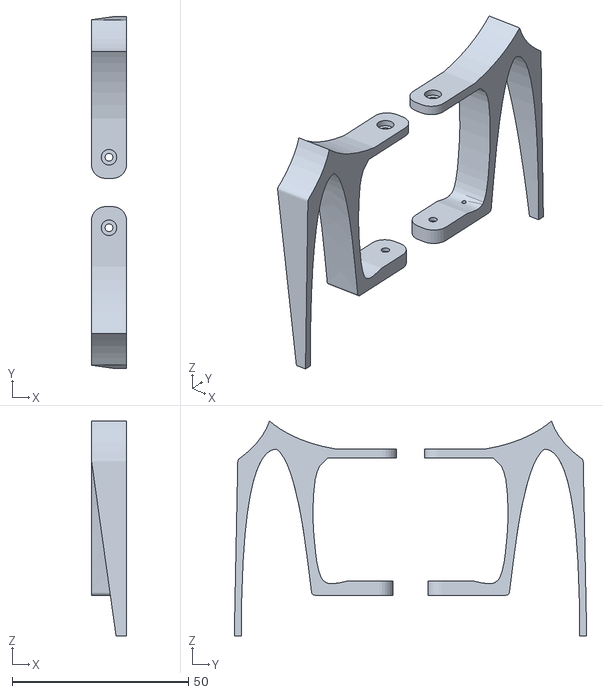
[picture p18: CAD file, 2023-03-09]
mods/c_wartmann/STL/RobaslingBlender-leg_rear_cw.stl
10.0 x 100.0 x 61.0

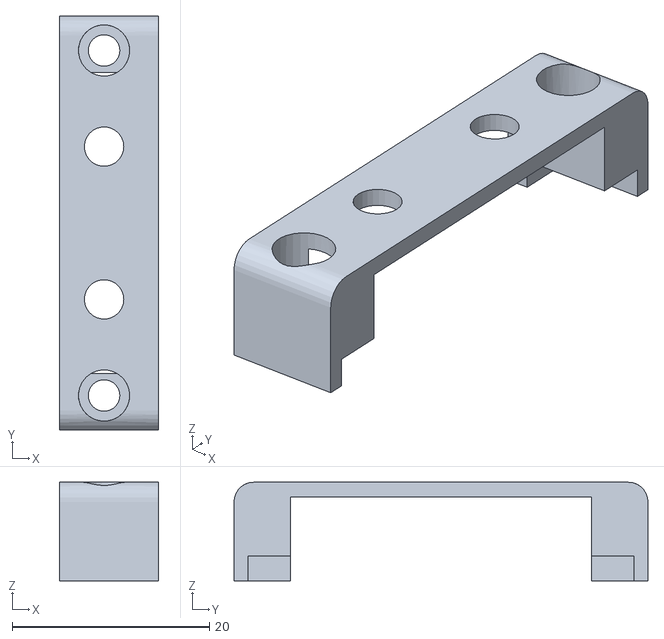
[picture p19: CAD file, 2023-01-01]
printed_parts/sensor_bank_scd41.stl
10.0 x 42.0 x 10.0

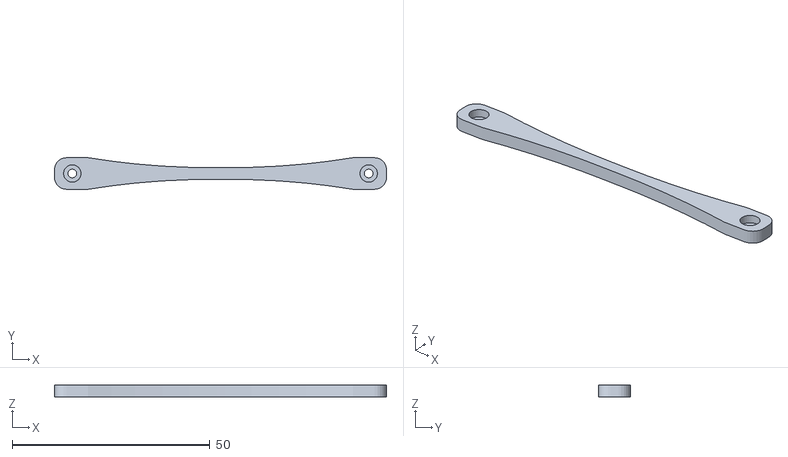
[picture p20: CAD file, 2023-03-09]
mods/c_wartmann/STL/RobaslingBlender-bar_medium_cw.stl
84.0 x 8.00 x 3.00

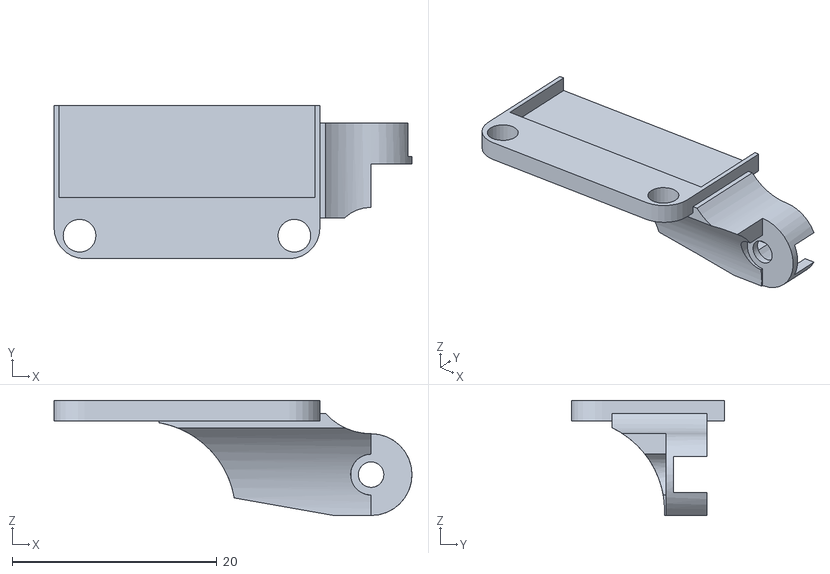
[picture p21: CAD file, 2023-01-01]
printed_parts/screen_holder.stl
35.0 x 15.0 x 11.2

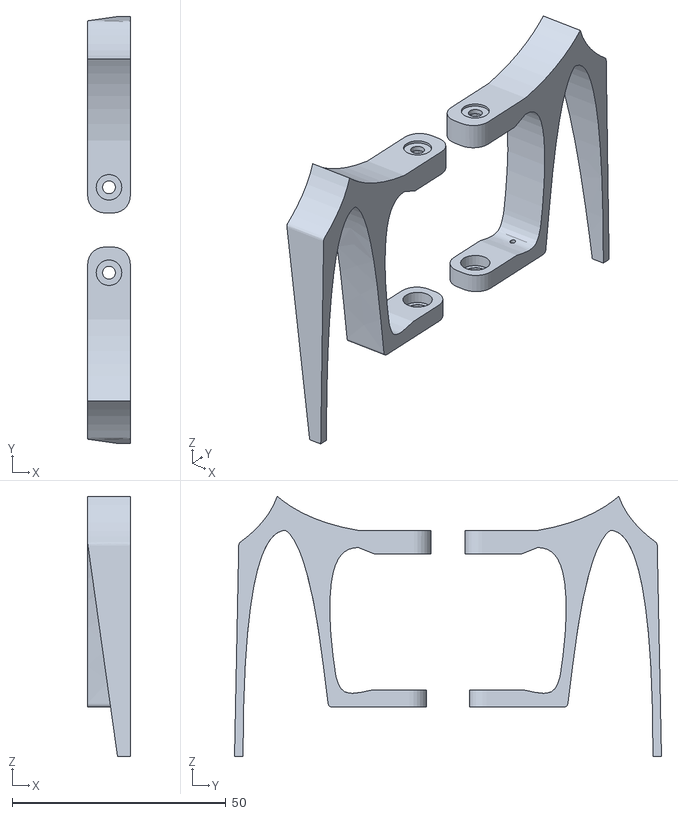
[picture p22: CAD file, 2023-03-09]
mods/c_wartmann/STL/RobaslingBlender-leg_front_right_cw.stl
10.0 x 100.0 x 61.0

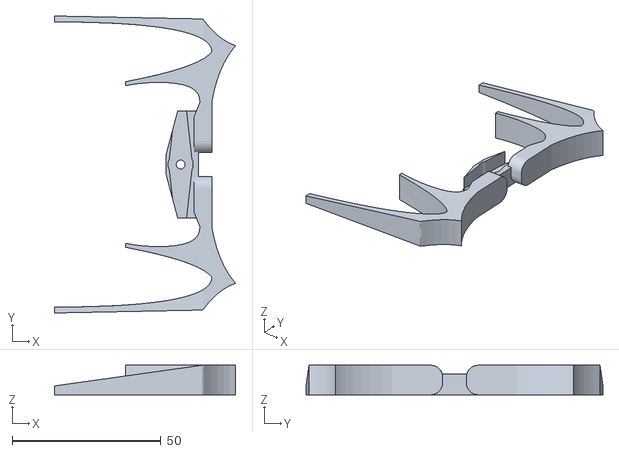
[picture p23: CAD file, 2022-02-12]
printed_parts/leg_centre.stl
61.0 x 100.0 x 10.0

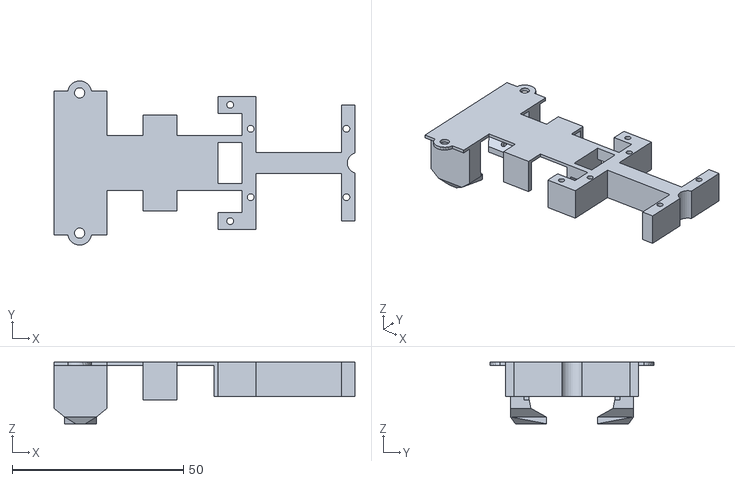
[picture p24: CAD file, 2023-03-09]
mods/c_wartmann/STL/RobaslingBlender-rear_bottom_cw.stl
88.0 x 48.0 x 18.0

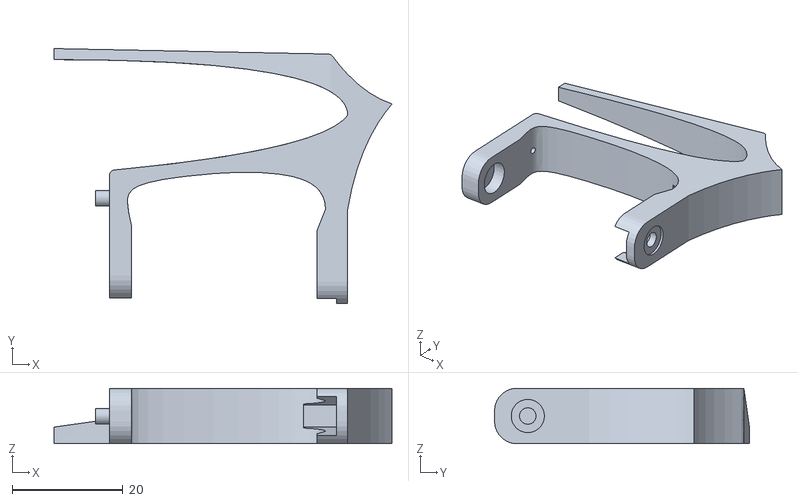
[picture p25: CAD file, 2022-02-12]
printed_parts/leg_front_left.stl
61.0 x 46.0 x 10.00

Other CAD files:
mods/c_wartmann/STL/RobaslingBlender-base.stl
printed_parts/rear_bottom_lipo1000.stl
mods/c_wartmann/STL/RobaslingBlender-rear_bank_cw.stl
printed_parts/front_bottom.stl
mods/c_wartmann/RobaslingBlender.blend
printed_parts/bar.stl
printed_parts/bar_long.stl
printed_parts/bar_medium.stl
printed_parts/base.stl
printed_parts/board_carrier.stl
printed_parts/deprecated/board_carrier.stl
printed_parts/deprecated/rear_bottom.stl
printed_parts/leg_front_right.stl
printed_parts/leg_rear_left.stl
printed_parts/leg_rear_right.stl
printed_parts/mods_c_otto/Adapterplatte.stl
printed_parts/mods_c_otto/ToF Sensor.stl
printed_parts/rear_bank.stl
printed_parts/rear_bottom.stl
printed_parts/sensor_adapter_evo_mini_terabee.stl
printed_parts/sensor_arm.stl

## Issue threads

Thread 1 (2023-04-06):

Link to VL53L0X Code missing

HMSteve, 2023-04-06:
Waere super, wenn der Link im Wiki unter [https://github.com/teuler/robotling2/wiki/Sensoren#time-of-flight-sensoren](url) ergaenzt werden koennte. Vielen Dank!

teuler, 2023-04-07:
Danke für den Hinweis. Habe ich ergänzt. Liegt aber nur als MicroPython code vor. Eine MMBasic-Version sollte aber nicht allzu schwierig sein.

Closed 2023-04-07.

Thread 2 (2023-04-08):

Gerber Files

AxelAhlborn, 2023-04-08:
Hallo,
gibt es Gerber Files für die Platine ?
MfG Axel Ahlborn

teuler, 2023-04-10:
Hallo Axel,
habe ich nun hinzugefügt. Ich habe sie aus Fritzing exportiert, ich habe sie allerdings noch nie ausprobiert - die Platinen habe ich bisher immer direkt aus der Fritzing-Datei herstellen lassen.
VGT

teuler, 2023-04-10:
Falls irgenwelche Probleme mit den Gerber files auftreten wäre ich für einen Hinweis dankbar :-)

AxelAhlborn, 2023-04-10:
Hallo, vielen Dank für die Gerber Files. Ich konnte heute das ZIP Archiv
ohne Probleme bei JLCPCB einchecken und bestellen. Somit gehe ich davon
aus, dass alles i.O. ist. Ich werde für das Projekt etwas brauchen, da der
Sommer kommt und so etwas eher für die kalte Jahreszeit ist.
MFG Axel Ahlborn

Thomas Euler ***@***.***> schrieb am Mo., 10. Apr. 2023,
11:15:

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

HMSteve, 2023-04-22:
> Falls irgenwelche Probleme mit den Gerber files auftreten wäre ich für einen Hinweis dankbar :-)

Habe auf Basis der Gerber files bei JLC bestellt und gestern bestueckt, Platine sieht gut aus und der Robotling laeuft damit. Danke fuers Teilen🙂

teuler, 2023-04-22:
Sehr schön - danke fürs Feedback

Closed 2023-04-29.

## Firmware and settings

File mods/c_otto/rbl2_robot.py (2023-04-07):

# ----------------------------------------------------------------------------
# rbl2_robot.py
#
# Representation of the robot
#
# The MIT License (MIT)
# Copyright (c) 2021 Thomas Euler
# 2021-04-03, v1.0
# ----------------------------------------------------------------------------
import time
import array
import utime
from machine import Pin, I2C, ADC
import micropython
              
from robotling_lib.platform.rp2 import board_rp2 as board
from vl53l0x import setup_tofl_device, TBOOT
import rbl2_gui
import rbl2_config as cfg
import rbl2_global as glb
import rbl2_gait as gait

# pylint: disable=bad-whitespace
__version__  = "0.1.0.0"

# Global variables to communicate with task on core 1
# (Do not access other than via the `RobotBase` instance!!)
g_state_gait = glb.STATE_NONE
g_state      = glb.STATE_NONE
g_cmd        = glb.CMD_NONE
g_counter    = 0
g_dist_evo   = None
g_move_dir   = 0.
g_move_vel   = 2
g_do_exit    = False
g_led        = Pin(board.D11, Pin.OUT)
    
# pylint: enable=bad-whitespace

# ----------------------------------------------------------------------------
class Robot(object):
  """Robot representation"""

  def __init__(self, core=1, use_gui=True, verbose=False):
    global g_state
    global g_dist_tof
    global tofl0, tofl1, tofl2
    global g_gui
    global g_gait

    g_gui = rbl2_gui.GUI()
    g_gait = gait.Gait()
    # Initializing ...
    g_state = glb.STATE_NONE
    self._verbose = verbose
    self._core = core
    self._spin_period_ms = 0
    self._spin_t_last_ms = 0
    self._do_autoupdate_gui = False
    self._no_servos = False

    # Initializing some hardware
    self._pinVBUSPresent = Pin(board.VBUS, Pin.IN)
    self._pinPower_V = ADC(Pin(board.BAT))

    # Initialize picodisplay, if any
    if g_gui:
      g_gui.clear()
      g_gui.LED.startPulse(150)
      g_gui.on(True)
      g_gui.show_version()
      g_gui.show_general_info("n/a")

    # Initialize devices
    if "VL53L0x" in cfg.DEVICES:
        device_1_xshut = Pin(cfg.TOFL_SHUT_1, Pin.OUT)
        device_2_xshut = Pin(cfg.TOFL_SHUT_2, Pin.OUT)
        device_1_xshut.value(1)
        device_2_xshut.value(1)
        utime.sleep_us (TBOOT)
        i2c = I2C(id=cfg.TOFL_I2C, sda=Pin(cfg.TOFL_SDA), scl=Pin(cfg.TOFL_SCL))

        addresses =i2c.scan()
        if (not (0x31 in addresses)):
#            print("Setting up device 0")
            device_1_xshut.value(0)
            device_2_xshut.value(0)
            tofl0 = setup_tofl_device(i2c, 40000, 12, 8)
            tofl0.set_address(0x31)
        else:
#            print("Reconnect device 0")
            device_1_xshut.value(0)
            device_2_xshut.value(0)
            tofl0 = setup_tofl_device(i2c, 40000, 12, 8, 0x31)

        if (not (0x33 in addresses)):
#            print("Setting up device 1")
            device_1_xshut.value(1)
            device_2_xshut.value(0)
            utime.sleep_us(TBOOT)
            tofl1 = setup_tofl_device(i2c, 40000, 12, 8)
            tofl1.set_address(0x33)
        else:
#            print("Reconnect device 1")
            device_1_xshut.value(1)
            device_2_xshut.value(0)
            utime.sleep_us(TBOOT)
            tofl1 = setup_tofl_device(i2c, 40000, 12, 8, 0x33)

        if (0x29 in addresses):
#            print("Now setting up device 2")
            # Re-enable device 2 - on the same bus
            device_1_xshut.value(1)
            device_2_xshut.value(1)
            utime.sleep_us(TBOOT)
            tofl2 = setup_tofl_device(i2c, 40000, 12, 8)
        else:
            print("!!!!Fehler!!!")
            
        g_dist_tof = True

    # Depending on `core`, the thread that updates the hardware either runs
    # on the second core (`core` == 1) or on the same core as the main program
    # (`core` == 0). In the latter case, the classes `sleep_ms()` function
    # needs to be used and called frequencly to keep the hardware updated.
    if self._core == 1:
      # Starting hardware thread on core 1 and wait until it is ready
      import _thread
      self._Task = _thread.start_new_thread(self._task_core1, ())
      glb.toLog("Hardware thread on core 1 starting ...")
      while not g_state_gait == glb.STATE_IDLE:
        time.sleep_ms(50)
      glb.toLog("Hardware thread ready.")
    else:
      # Do not use core 1 for hardware thread; instead the main loop has to
      # call `sleep_ms()` frequently. Here, prime that sleep function ...
      self.sleep_ms(period_ms=cfg.MIN_UPDATE_MS, callback=self._task_core0)
      glb.toLog("Hardware co-uses core 0.")

    g_state = glb.STATE_IDLE

  # - - - - - - - - - - - - - - - - - - - - - - - - - - - - - - - - - - - - -
  def deinit(self):
    if g_gui:
      g_gui.deinit()
      g_gui.LED.RGB = (60,0,0)
    if g_dist_tof:
      tofl0.set_address(0x29)
      tofl1.set_address(0x29)
    if g_state is not glb.STATE_OFF:
      self.power_down()
      counter = 0
      while g_state is not glb.STATE_OFF:
        assert counter > 1000, "Locked in `RobotBase.deinit`"
        counter += 1
        self.sleep_ms(50)


  # - - - - - - - - - - - - - - - - - - - - - - - - - - - - - - - - - - - - -
  @property
  def state(self):
    """ Returns `state` as a constant `STATE_xxx` (defined in `rbl2_global.py`)
    """
    return g_state

  @property
  def direction(self):
    """ Returns current movement direction (see `turn()` for details)
    """
    return g_move_dir

  @property
  def distances_mm(self):
    """ Returns the distances (in [mm]) as an array. The lengths of the array
        depends on the sensor: e.g. the vl53l0x reports 1 value, 3 times.
    """
    if g_dist_tof:
        _d = array.array('i', (0 for _ in range(3)))
        _d[0] = tofl2.ping()
        _d[1] = tofl0.ping()
        _d[2] = tofl1.ping()
#        _d = [150, 150, 150]
        return _d
    else:
        return []

  @property
  def is_connected_via_usb(self):
    """ Returns True if connected via USB cable (and VSYS is present)
    """
    return self._pinVBUSPresent.value()

  @property
  def power_V(self):
    """ Returns the input voltage that powers the microcontroller
    """
    return self._pinPower_V.read_u16()*3/65536*3.3

  # GUI-related properties
  @property
  def autoupdate_gui(self):
    """ Endable/disable autoupdate of GUI during `sleep_ms`
    """
    return self._do_autoupdate_gui
  @autoupdate_gui.setter
  def autoupdate_gui(self, val :bool):
    self._do_autoupdate_gui = val

  @property
  def is_pressed_A(self):
    return g_gui.display.is_pressed(g_gui.display.BUTTON_A) if g_gui else False

  # - - - - - - - - - - - - - - - - - - - - - - - - - - - - - - - - - - - - -
  def update_display(self):
    """ If display is connected, show important status information there
    """
    if g_gui:
      vbus = self._pinVBUSPresent.value()
      pw_V = self.power_V
      g_gui.show_general_info(glb.STATE_STRS[g_state],
          "{0:.1f}".format(g_move_dir) if g_state is glb.STATE_TURNING else "",
          vbus, pw_V
        )
      if g_dist_tof:
        g_gui.show_distance_tof(self.distances_mm)

  def show_message(self, msg):
    """ Show a message on the display
    """
    if g_gui:
      g_gui.show_msg(msg)

  # - - - - - - - - - - - - - - - - - - - - - - - - - - - - - - - - - - - - -
  def move_forward(self, wait_for_idle=False):
    """ Move straight forward using current gait and velocity.
        If `wait_for_idle` is True, then trigger action only when idle.
    """
    global g_cmd, g_move_dir
    if not wait_for_idle or g_state_gait == glb.STATE_IDLE:
      g_move_dir = 0.
      if not self._no_servos:
        g_cmd = glb.CMD_MOVE

  def turn(self, dir, wait_for_idle=False):
    """ Turn using current gait and velocity; making with `dir` < 0 a left and
        `dir` > 0 a right turn. The size of `dir` (1 >= |`dir`| > 0) giving
        the turning strength (e.g. 1.=turn in place, 0.2=walk in a shallow
        curve). If `wait_for_idle` is True, then trigger action only when idle.
    """
    global g_cmd, g_move_dir
    if not wait_for_idle or g_state_gait == glb.STATE_IDLE:
      g_move_dir = max(min(dir, 1.0), -1.0)
      if not self._no_servos:
        g_cmd = glb.CMD_MOVE

  def stop(self):
    """ Stop if walking
    """
    global g_cmd
    if g_state_gait in [glb.STATE_WALKING, glb.STATE_TURNING]:
      g_cmd = glb.CMD_STOP

  def turn_servos_off(self):
    g_gait._SM.turn_all_off()

  def no_servos(self, val):
    self._no_servos = val

  def power_down(self):
    """ Power down and end task
    """
    global g_cmd, g_move_dir
    glb.toLog("Request hardware thread power down ...")
    g_move_dir = 0.
    g_cmd = glb.CMD_POWER_DOWN

  # - - - - - - - - - - - - - - - - - - - - - - - - - - - - - - - - - - - - -
  def sleep_ms(self, dur_ms=0, period_ms=-1, callback=None):
    """ This function is an alternative to `time.sleep_ms()`; it sleeps but
        also  keep the robot's hardware updated.
        e.g. "sleep_ms(period_ms=50, callback=myfunction)"" is setting it up,
             "sleep_ms(100)"" (~sleep for 100 ms) or "sleep_ms()" keeps it
             running.
    """
    if self._spin_period_ms > 0:
      p_ms = self._spin_period_ms
      p_us = p_ms *1000
      d_us = dur_ms *1000

      if dur_ms > 0 and dur_ms < (p_ms -cfg.APPROX_SPIN_MS):
        time.sleep_ms(int(dur_ms))

      elif dur_ms >= (p_ms -cfg.APPROX_SPIN_MS):
        # Sleep for given time while updating the board regularily; start by
        # sleeping for the remainder of the time to the next update ...
        t_us  = time.ticks_us()
        dt_ms = time.ticks_diff(time.ticks_ms(), self._spin_t_last_ms)
        if dt_ms > 0 and dt_ms < p_ms:
          time.sleep_ms(dt_ms)

        # Update
        self._spin_callback()
        if self._do_autoupdate_gui:
          self.update_display()
        self._spin_t_last_ms = time.ticks_ms()

        # Check if sleep time is left ...
        d_us = d_us -int(time.ticks_diff(time.ticks_us(), t_us))
        if d_us <= 0:
          return

        # ... and if so, pass the remaining time by updating at regular
        # intervals
        while time.ticks_diff(time.ticks_us(), t_us) < (d_us -p_us):
          time.sleep_us(p_us)
          self._spin_callback()
          if self._do_autoupdate_gui:
            self.update_display()

        # Remember time of last update
        self._spin_t_last_ms = time.ticks_ms()

      else:
        # No sleep duration given, thus just check if time is up and if so,
        # call update and remember time
        d_ms = time.ticks_diff(time.ticks_ms(), self._spin_t_last_ms)
        if d_ms > self._spin_period_ms:
          self._spin_callback()
          if self._do_autoupdate_gui:
            self.update_display()
          self._spin_t_last_ms = time.ticks_ms()

    elif period_ms > 0:
      # Set up spin parameters and return
      self._spin_period_ms = period_ms
      self._spin_callback = callback
      self._spin_t_last_ms = time.ticks_ms()
    else:
      # Spin parameters not setup, therefore just sleep
      time.sleep_ms(dur_ms)

  # - - - - - - - - - - - - - - - - - - - - - - - - - - - - - - - - - - - - -
  def _task_core0(self):
    """ This is the core 0-version of the routine that keeps the hardware
        updated and responds to commands (e.g. move, turn).
        - It is called by `sleep_ms()`.
        - It uses only global variables for external objects to stay
          compatible with the core-1 version below.
    """
    global g_state_gait, g_state, g_counter
    global g_cmd, g_do_exit

    if g_state == glb.STATE_OFF:
      return
    if g_state is not glb.STATE_POWERING_DOWN:
      g_led.value(1)

      # Handle new command, if any ...
      if g_cmd is not glb.CMD_NONE:

        if g_cmd == glb.CMD_MOVE:
          g_gait.direction = g_move_dir
          g_gait.walk()
          g_state = glb.STATE_WALKING if g_move_dir == 0 else glb.STATE_TURNING

        if g_cmd in [glb.CMD_STOP, glb.CMD_POWER_DOWN]:
          # Stop or power down ...
          g_gait.stop()
          g_state = glb.STATE_STOPPING
          g_do_exit = g_cmd == glb.CMD_POWER_DOWN

        g_cmd = glb.CMD_NONE

      # Wait for transitions to update state accordingly ...
      if g_state == glb.STATE_STOPPING and g_state_gait == glb.STATE_IDLE:
        g_state = glb.STATE_IDLE
      if g_state == glb.STATE_IDLE and g_do_exit:
        g_state = glb.STATE_POWERING_DOWN

      # Spin everyone who needs spinning
      g_gait.spin()
      g_state_gait = g_gait.state
      if g_dist_evo:
        g_dist_evo.update(raw=True)
      if g_gui:
        g_gui.spin()
      g_counter += 1
      g_led.value(0)

    else:
      # Finalize ...
      g_gait.deinit()
      g_led.value(0)
      g_state = glb.STATE_OFF

  # - - - - - - - - - - - - - - - - - - - - - - - - - - - - - - - - - - - - -
  @staticmethod
  def _task_core1():
    """ This is the core 1-version of the routine that keeps the hardware
        updated and responds to commands (e.g. move, turn).
        - It runs independently on core 1; in parallel to the main program on
          core 0.
        - It communicates via global variables.
    """
    global g_state_gait, g_state, g_counter
    global g_cmd, g_do_exit

    # Loop
    g_do_exit = False
    try:
      try:
        g_state_gait = glb.STATE_IDLE

        # Main loop ...
        while g_state is not glb.STATE_POWERING_DOWN:
          g_led.value(1)

          # Handle new command, if any ...
          if g_cmd is not glb.CMD_NONE:

            if g_cmd == glb.CMD_MOVE:
              g_gait.direction = g_move_dir
              g_gait.walk()
              if g_move_dir == 0:
                g_state = glb.STATE_WALKING
              else:
                g_state = glb.STATE_TURNING

            if g_cmd == glb.CMD_STOP:
              g_gait.stop()
              g_state = glb.STATE_STOPPING

            if g_cmd == glb.CMD_POWER_DOWN:
              # Stop and power down ...
              g_gait.stop()
              g_do_exit = True

            g_cmd = glb.CMD_NONE

          # Wait for transitions to update state accordingly ...
          if g_state == glb.STATE_STOPPING and g_state_gait == glb.STATE_IDLE:
            g_state = glb.STATE_IDLE
          if g_state == glb.STATE_IDLE and g_do_exit:
            g_state = glb.STATE_POWERING_DOWN

          # Spin everyone who needs spinning
          g_gait.spin()
          g_state_gait = g_gait.state
          if g_dist_evo:
            g_dist_evo.update(raw=False)
          g_gui.spin()
          g_counter += 1
          g_led.value(0)

          # Wait for a little while
          time.sleep_ms(25)

      except KeyboardInterrupt:
        pass

    finally:
      g_gait.deinit()
      g_led.value(0)
      glb.toLog("Hardware thread ended.")
      g_state = glb.STATE_OFF

# ----------------------------------------------------------------------------
if __name__ == "__main__":
# Initialize robot
  micropython.mem_info()
  Robot = Robot(core=cfg.HW_CORE)
  Robot.autoupdate_gui = True
  micropython.mem_info()

  print("Press `A` for sensors only ...")
  trials = 80
  only_sensors = False 
  while trials > 0:
    if Robot.is_pressed_A:
      only_sensors = True
      break
    trials -= 1
    time.sleep_ms(25)
  if only_sensors:
    Robot.show_message("sensors-only")
    print ("Sensors  Only")
    Robot.no_servos(only_sensors)
  try:
    while not Robot.state == glb.STATE_OFF:
      dL, dC, dR = Robot.distances_mm

      if not only_sensors:
        objL = (dL < 80) or (dC < 80)
        objR = (dR < 80) or (dC < 80)
        clfL = (dL > 200) or (dC > 200)
        clfR = (dR > 200) or (dC > 200)
        free = not objL and not objR and not clfL and not clfR

        if free:
          if Robot.state is not glb.STATE_WALKING:
            Robot.move_forward()
            Robot.show_message("-")
        else:
          Robot.stop()
          while Robot.state is not glb.STATE_IDLE: Robot.sleep_ms(25)

          if clfL or clfR:
            if clfL and not clfR:
              Robot.turn(+1)
              Robot.show_message("Cliff_L__")
            elif not clfL and clfR:
              Robot.turn(-1)
              Robot.show_message("Cliff___R")
            elif clfL and clfR:
              Robot.turn(-1)
              Robot.show_message("Cliff__C_")
            Robot.sleep_ms(4000)

          elif objL or objR:
            if objL and not objR:
              Robot.turn(+1)
              Robot.show_message("Objct_L__")
            elif not objL and objR:
              Robot.turn(-1)
              Robot.show_message("Objct___R")
            elif objL and objR:
              Robot.turn(-1)
              Robot.show_message("Objct__C_")
            Robot.sleep_ms(2000)

      # Sleep for a while and, if running only on one core, make sure that
      # the robot's hardware is updated
      Robot.sleep_ms(50)

  except KeyboardInterrupt:
    # Clean up
    Robot.deinit()

# ----------------------------------------------------------------------------
 

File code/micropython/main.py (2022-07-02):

# ----------------------------------------------------------------------------
# main.py
#
# Main program
#
# The MIT License (MIT)
# Copyright (c) 2021-2022 Thomas Euler
# 2021-03-28, v1.0
# 2022-02-12, v1.1
# 2022-04-08, v1.2, a few improvements and fixes
# ----------------------------------------------------------------------------
import gc
import time
import random
import rbl2_robot
import rbl2_global as glb
import rbl2_config as cfg
from micropython import const

# pylint: disable=bad-whitespace
DIST_TOF_OBJ    = const(35)   # object if smaller than this distance
DIST_TOF_CLIFF  = const(150)  # cliff if larger than this distance
# pylint: enable=bad-whitespace

# ----------------------------------------------------------------------------
if __name__ == "__main__":
  # Initialize robot
  is_gui = "display" in cfg.DEVICES
  Robot = rbl2_robot.Robot(core=cfg.HW_CORE, use_gui=is_gui)
  Robot.autoupdate_gui = True
  only_sensors = False
  is_running = True

  # Wait for user to start robot, if display with button available
  if is_gui and cfg.DISPLAY_TYPE in [cfg.PIMORONI_PICO_DISPLAY]:
    glb.toLog("Press `A` to start robot ...")
    while True:
      if Robot.is_pressed_A:
        break
      time.sleep_ms(25)

  # Main loop
  glb.toLog("Starting main loop (press `X` to shutdown)")
  try:
    while not Robot.state == glb.STATE_OFF and is_running:

      # Get distance sensor readings depending on sensor type and calculate
      # if obstacles and/or cliffs are detected ...
      if Robot.distance_sensor_type == cfg.STY_EVOMINI:
        dLLo, dLHi, dRLo, dRHi = Robot.distances_mm
        objL = (dLLo > 0 and dLLo < 65) or (dLHi > 0 and dLHi < 80)
        objR = (dRLo > 0 and dRLo < 65) or (dRHi > 0 and dRHi < 80)
        objC = objL and objR
        clfL = dLLo > 120
        clfR = dRLo > 120
        free = not objL and not objR and not objC and not clfL and not clfR

      elif Robot.distance_sensor_type == cfg.STY_TOF:
        dL, dC, dR = Robot.distances_mm
        #print(dL, dC, dR)
        objL = (dL > 0 and dL < DIST_TOF_OBJ)
        objC = (dC > 0 and dC < DIST_TOF_OBJ)
        objR = (dR > 0 and dR < DIST_TOF_OBJ)
        clfL = dL > DIST_TOF_CLIFF
        clfR = dR > DIST_TOF_CLIFF
        free = not objL and not objR and not objC and not clfL and not clfR

      if only_sensors:
        # If only testing sensors, skip rest of main loop
        continue

      # Act on detected objects and/or cliffs
      if free:
        if Robot.state is not glb.STATE_WALKING:
          Robot.move_forward()
          Robot.show_message("-")
      else:
        Robot.stop()
        while Robot.state is not glb.STATE_IDLE:
          Robot.sleep_ms(25)

        if clfL or clfR:
          if clfL and not clfR:
            Robot.turn(+1)
            Robot.show_message("Cliff_L__")
          elif not clfL and clfR:
            Robot.turn(-1)
            Robot.show_message("Cliff___R")
          elif clfL and clfR:
            Robot.move_backward()
            Robot.sleep_ms(2000)
            Robot.turn(1 if random.random() > 0.5 else -1)
            Robot.show_message("Cliff_L_R")
          Robot.sleep_ms(2000)

        elif objL or objC or objR :
          if objL and not objR:
            Robot.turn(+1)
            Robot.show_message("Objct_L__")
          elif not objL and objR:
            Robot.turn(-1)
            Robot.show_message("Objct___R")
          elif objC:
            Robot.move_backward()
            Robot.sleep_ms(1000)
            Robot.turn(1 if random.random() > 0.5 else -1)
            Robot.show_message("Objct__C_")
          Robot.sleep_ms(1000)

      # Sleep for a while and, if running only on one core, make sure that
      # the robot's hardware is updated
      Robot.sleep_ms(25)

      # Check if user pressed the X button
      is_running = not Robot.exit_requested

  except KeyboardInterrupt:
    pass

  # Clean up
  Robot.deinit()

# ----------------------------------------------------------------------------

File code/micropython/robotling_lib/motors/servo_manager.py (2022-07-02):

# ----------------------------------------------------------------------------
# servo_manager.py
# Class to manage and control a number of servos
#
# The MIT License (MIT)
# Copyright (c) 2020-2022 Thomas Euler
# 2020-01-03, v1
# 2020-08-02, v1.1 ulab
# 2020-10-31, v1.2, use `languageID` instead of `ID`
# 2021-02-14, v1.3, small improvements towards more performance
# 2021-02-28, v1.4, compatibility w/ rp2, no `ulab` for space reasons
# 2022-01-04, v1.5, Nano RP2040 Connect added, simplified (only linear)
# 2022-05-05, v1.6, Calibration code added
# 2022-05-08, v1.7, TRJ_LINEAR=Normal, TRJ_SINE=slow start and end move
# 2022-06-11, v1.8, Allow setting last position after power-off
# 2022-06-26, v1.8, Added option not to use `ulab`
# ----------------------------------------------------------------------------
import gc
import time
import array
from machine import Timer
from robotling_lib.misc.helpers import timed_function
from robotling_lib.platform.platform import platform as pf
import robotling_lib.misc.ansi_color as ansi
try:
  from ulab import numpy as np
  ULAB = True
except ImportError:
  import math as np
  ULAB = False

# pylint: disable=bad-whitespace
__version__        = "0.1.8.0"
RATE_MS            = const(10)  # 5=hangs, 15...20=ok, 25=not continues
HARDWARE_TIMER     = const(0)
# pylint: enable=bad-whitespace

# ----------------------------------------------------------------------------
class ServoManager(object):
  """Class to manage and control a number of servos"""
  # pylint: disable=bad-whitespace
  TYPE_NONE       = const(0)
  TYPE_HORIZONTAL = const(1)
  TYPE_VERTICAL   = const(2)
  TYPE_SENSOR     = const(3)

  TRJ_LINEAR      = const(0)
  TRJ_SINE        = const(1)
  # pylint: enable=bad-whitespace

  def __init__(self, n, verbose=False):
    """ Initialises the management structures
    """
    self._isVerbose = verbose
    self._nChan = max(1, n)
    self._Servos = [None]*n                               # Servo objects
    self._servo_type = bytearray([TYPE_NONE]*n)           # Servo type
    self._servo_number = bytearray([255]*n)               # Servo number
    self._servoPos = array.array("f", [0]*n)              # Servo pos [us]
    self._SIDList = bytearray([255]*n)                    # Servos to move next
    self._targetPosList = array.array("H", [0]*n)         # Target pos [us]
    self._currPosList = array.array("f", [-1]*n)          # Current pos [us]
    self._stepSizeList = array.array("f", [0]*n)          # .. step sizes [us]
    self._nToMove = 0                                     # # of servos to move
    self._dt_ms = 0                                       # Time period [ms]
    self._nSteps = 0                                      # countdown of steps to move
    self._trajNormList = array.array("f", [0]*n)          # Sensor norm factor (TRJ_SINE)
    self._iStep = 0                                       # Current step
    self._nStTotal = 0                                    # total # of steps
    self._mm18 = None
    self._isMoving = False
    self._isFirstMove = True
    self._Timer = Timer() if pf.isRP2 else Timer(HARDWARE_TIMER)

  def add_servo(self, i, servoObj, pos=0):
    """ Add at the entry `i` of the servo list the servo object, which has to
        define the following functions:
        - `write_us(t_us)`
        - `angle_in_us(value=None)`
        - `off()`
        - `deinit()`
    """
    if i in range(self._nChan):
      self._Servos[i] = servoObj
      self._servoPos[i] = servoObj.angle_in_us()
      self._servo_number[i] = i
      if self._isVerbose:
        print("Add servo #{0:-2.0f}, at {1} us"
              .format(i, int(self._servoPos[i])))
      try:
        self._mm18 = servoObj._mm18
      except AttributeError:
        pass

  def set_servo_type(self, i, type):
    """ Change servo type (see `TYPE_xxx`)
    """
    if i in range(self._nChan) and self._Servos[i] is not None:
      self._servo_type[i] = type

  def define_servo_pos(self, _pos):
    """ Define servo position (from angle) without moving the servo,
        e.g. to define the last starting position at power-off
    """
    if len(_pos) == self._nChan:
      for i in range(self._nChan):
        if self._Servos[i] is not None:
          t = self._Servos[i].angle_in_us(_pos[i])
          self._servoPos[i] = t
          self._currPosList[i] = t

  def turn_all_off(self, deinit=False):
    """ Turn all servos off
    """
    for servo in self._Servos:
      if not servo is None:
        servo.off()
        if deinit:
          servo.deinit()

  def deinit(self):
    """ Clean up
    """
    self._Timer.deinit()
    self.turn_all_off(deinit=True)

  # - - - - - - - - - - - - - - - - - - - - - - - - - - - - - - - - - - - - -
  @timed_function
  def move_timed(self, servos, pos, dt_ms=0):
    self.move(servos, pos, dt_ms, lin_vel)

  #@micropython.native
  def move(self, servos, pos, dt_ms=0, traject=TRJ_LINEAR):
    """ Move the servos in the list to the positions given in `pos`.
        If `dt_ms` > 0, then it will be attempted that all servos reach the
        position at the same time (that is after `dt_ms` ms)
    """
    # Stop ongoing move
    self._isMoving = False

    # Prepare new move
    n = 0
    trj = traject
    nSteps = dt_ms /RATE_MS
    ser = self._Servos
    sdl = self._SIDList
    tpl = self._targetPosList
    spo = self._servoPos
    ssl = self._stepSizeList
    cpl = self._currPosList
    tnl = self._trajNormList
    for iSr, SID in enumerate(servos):
      if not ser[SID]:
        continue
      sdl[n] = SID
      tpl[n] = ser[SID].angle_in_us(pos[iSr])
      if nSteps > 0:
        # A time period is given, therefore calculate the step sizes for this
        # servo's move, with ...
        p = spo[SID]
        if traject == TRJ_SINE:
          ssl[n] = tpl[n] -p  # whole step
          cpl[n] = p          # current position
          if ULAB:
            _a = np.array(
                [np.sin((i+1)/nSteps*np.pi) for i in range(int(nSteps-1))]
              )
            tnl[n] = np.sum(_a) # sum of sine values
          else:
            _a = array.array(
                "f",
                [np.sin((i+1)/nSteps*math.pi) for i in range(int(nSteps-1))]
              )
            tnl[n] = 0
            for j in range(len(_a)):
              tnl[n] += _a[j]
        else:
          # Linear move (each step has the same size)
          s = (tpl[n] -p) /nSteps
          cpl[n] = int(p +s)
          ssl[n] = s
      else:
        # Move directly, therefore update already the final position
        spo[SID] = tpl[iSr]
      n += 1
    self._traject = traject
    self._iStep = 0
    self._nToMove = n
    self._dt_ms = dt_ms
    self._nSteps = int(nSteps)
    self._nStTotal = self._nSteps
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

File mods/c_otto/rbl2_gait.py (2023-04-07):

# ----------------------------------------------------------------------------
# rbl2_gait.py
#
# Gait control for robotling2
#
# The MIT License (MIT)
# Copyright (c) 2021 Thomas Euler
# 2021-03-03, v1.0
# ----------------------------------------------------------------------------
import time
import array
import rbl2_global as glb
import rbl2_config as cfg
from micropython import const
from robotling_lib.motors.servo import Servo
from robotling_lib.motors.servo_manager import ServoManager

# pylint: disable=bad-whitespace
__version__  = "0.1.0.0"

#                Servos,  Positions, Dur, Mode,           Next, Jump
GAIT_SEQ     = [([2],     [ 20],     250, glb.STATE_WALKING,   1,   4),     # 0
                ([0,1],   [ 40, 40], 400, glb.STATE_WALKING,   2,   None),  # 1
                ([2],     [-20],     250, glb.STATE_WALKING,   3,   4),     # 2
                ([0,1],   [-40,-40], 400, glb.STATE_WALKING,   0,   None),  # 3
                ([0,1],   [  0,  0], 400, glb.STATE_STOPPING,  5,   5),     # 4
                ([2],     [  0],     400, glb.STATE_STOPPING, -1,  None)]   # 5
GS_SRV       = const(0)
GS_POS       = const(1)
GS_DUR       = const(2)
GS_MODE      = const(3)
GS_NEXT      = const(4)
GS_JUMP      = const(5)
# pylint: enable=bad-whitespace

# ----------------------------------------------------------------------------
class Gait(object):
  """Gait control"""

  def __init__(self, verbose=False):
    # Initializing ...
    self._state = glb.STATE_NONE
    self._iStep = 0
    self._vel = 1.
    self._dir = 0.
    self._verbose = verbose

    # Configure servos and servo manager
    self._Servos = []
    self._SM = ServoManager(len(cfg.SRV_ID))
    for i, pin in enumerate(cfg.SRV_PIN):
      srv = Servo(pin, us_range=cfg.SRV_RANGE_US[i],
                  ang_range=cfg.SRV_RANGE_DEG[i])
#      print (pin, cfg.SRV_RANGE_US[i], cfg.SRV_RANGE_DEG[i])
      self._Servos.append(srv)
      self._SM.add_servo(cfg.SRV_ID[i], srv)

    # Getting ready
    self.neutral()
    time.sleep_ms(1000)
    self._state = glb.STATE_IDLE
    if self._verbose:
      glb.toLog("Gait control ready.")

  def deinit(self):
    """ Shutting down gait control
    """
    self._state = glb.STATE_POWERING_DOWN
    self.neutral(dt=500)
    time.sleep_ms(550)
    self._SM.deinit()
    if self._verbose:
      glb.toLog("Gait control off.")
    self._state = glb.STATE_OFF

  # - - - - - - - - - - - - - - - - - - - - - - - - - - - - - - - - - - - - -
  def neutral(self, dt=0):
    """ Assume neutral position
    """
    if self._verbose:
      print("Assuming neutral position ...")
    self._SM.move([0,1,2], [0,0,0], dt)

  # - - - - - - - - - - - - - - - - - - - - - - - - - - - - - - - - - - - - -
  def walk(self):
    """ Start walking, defined by the properties `direction` (e.g. -1=left
        turn, +1=right turn, 0=straight forward) and `velocity` (<0, slower,
        >1 faster)
    """
    self._state = glb.STATE_WALKING if self._dir == 0 else glb.STATE_TURNING
    self._iStep = 0
    self.spin()

  # - - - - - - - - - - - - - - - - - - - - - - - - - - - - - - - - - - - - -
  def stop(self):
    """ Stop movement gracefully
    """
    self._state = glb.STATE_STOPPING
    self.spin()

  # - - - - - - - - - - - - - - - - - - - - - - - - - - - - - - - - - - - - -
  def spin(self):
    """ Keep robot moving; needs to be called frequently
    """
    st = self._state
    sm = self._SM
    if st == glb.STATE_IDLE or sm.is_moving:
      return

    iS = self._iStep
    dr = self._dir
    if st in [glb.STATE_WALKING, glb.STATE_TURNING, glb.STATE_STOPPING]:
      # Apply direction
      pos = array.array("f", GAIT_SEQ[iS][GS_POS])
      for j, id in enumerate(GAIT_SEQ[iS][GS_SRV]):
        if dr < 0:
          if id == 0:
            pos[j] *= -abs(dr)
        elif dr > 0:
          if id == 1:
            pos[j] *= -abs(dr)

      # Execute move
      vel = int(GAIT_SEQ[iS][GS_DUR] *self._vel)
      sm.move(GAIT_SEQ[iS][GS_SRV], pos, vel)
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

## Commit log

2021-04-07 Board and parts
    [bar.stl, bar_long.stl, bar_medium.stl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]
2021-04-10 PCB updated
    [robotling2_v3.fzz]
2021-04-25 New STL files
    [base.stl, board_carrier.stl, rbl2_v13.FCStd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]
2021-05-09 Holder for LiPo adapted
    [rear_bottom_lipo1000.stl]
2021-05-09 Code update
    [foot_left.stl, foot_right.stl]
2021-12-16 Board update
    [robotling2_v4.fzz]
2022-02-12 Parts updated
    [sensor_adapter_evo_mini_terabee.stl, sensor_adapter_tof_pololu.stl, sensor_arm.stl]
2022-02-12 Parts turned into print position
    [front_bottom.stl, leg_centre.stl, leg_front_left.stl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]
2022-02-13 New parts
    [Adapterplatte.FCStd, ToF Sensor.FCStd]
2022-04-15 Pololu distance sensor w/PIO
2023-01-01 Update code and .stl files
    [board_carrier_v2.stl, screen_holder.stl, sensor_bank.stl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]
2023-03-09 CAW mod files added
    [RobaslingBlender-Akku_Platte.stl, RobaslingBlender-bar_medium_cw.stl, RobaslingBlender-base.stl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]
2023-03-12 Update
    PWM commands towards end
2023-04-08 Calibration program updated
2023-04-10 Gerber files added (and small stuff)
    [robotling2_v4.fzz]
